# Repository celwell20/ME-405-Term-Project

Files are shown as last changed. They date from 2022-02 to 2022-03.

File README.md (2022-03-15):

# ME 405 Term Project
## Tyler McCue and Clayton Elwell Term Project

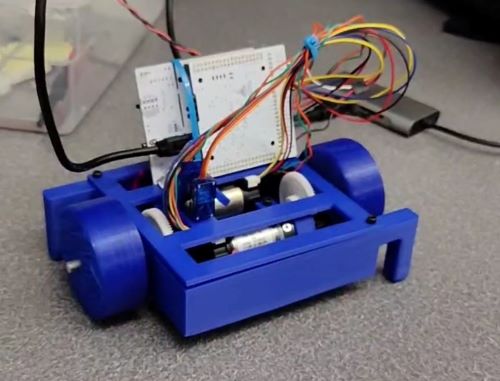
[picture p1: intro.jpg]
Intro


### Introduction
The purpose of this device is to draw a 2D image that may be determined by the user, or an appropriate
.hpgl interpreter. The device was not designed for a particular use case, rather as a novel mechatronic
system that can perform the desired task. Design constraints for this project included the project budget
and system complexity.

### Hardware
To address the small project budget, we sourced most of our hardware components from the various scrap piles
around the mechatronics lab. The large system components such as the wheel and chassis were 3D printed so that
we may iterate rapidly if need be. The only purchased components for this project are the bearings that
facilitate the wheels’ motion.

The system relies on two Pittman motors to actuate corresponding wheels that are linked via a simple gear train,
as seen in Figure 1. The wheels are 3D printed from TPU to increase friction and improve positional accuracy;
the chassis is fabricated from PLA. The two pegs on either side of the chassis help the car balance and prevent
the need for any software to balance the wheels with the motor torques (Figure 2). Two bearings facilitate each wheel’s
rotation, and the driveshafts are cut from 0.25” steel rod stock that was found in the mechatronics lab (Figure 3).

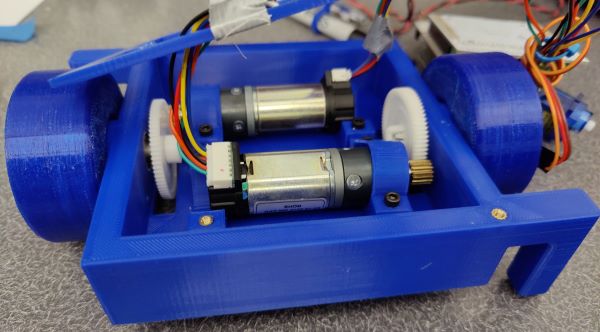
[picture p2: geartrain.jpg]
Pittman

<br>
Figure 1. Torque transmission system.

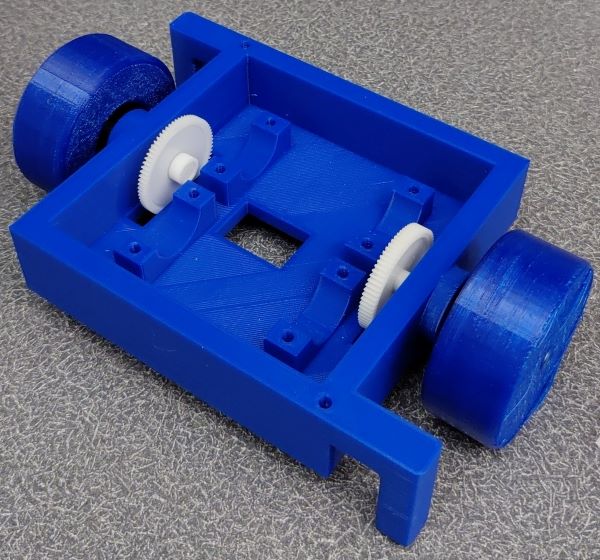
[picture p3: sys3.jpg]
Chassis

<br>
Figure 2. Chassis and wheels.

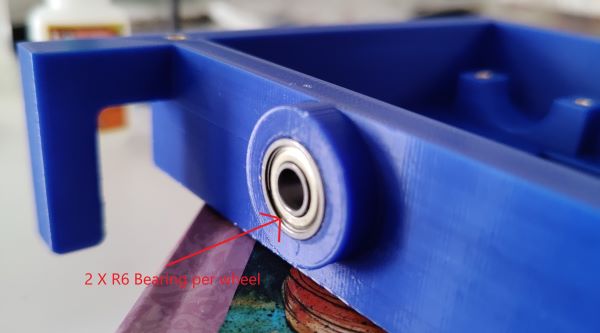
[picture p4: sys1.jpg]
Bearings

<br>
Figure 3. Press-fit bearings (with superglue).

To connect the motors to the chassis, M3 heat-set inserts and machine screws were used with PLA “straps” as
seen in Figure 1 (PLA straps) and 4 (heat-set inserts).

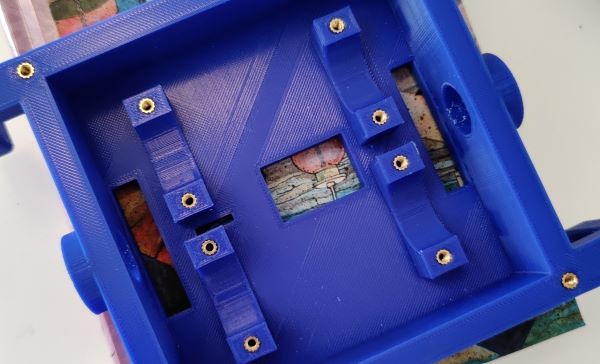
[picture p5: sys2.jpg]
Inserts

<br>
Figure 4. Chassis heat set inserts.

A Tower Pro servo motor is used control the drawing apparatus’s contact with the sketching surface; it is
press fit into a thin PLA plate that fastens to the chassis with M3 heat-set inserts and machine screws (Figure 5).

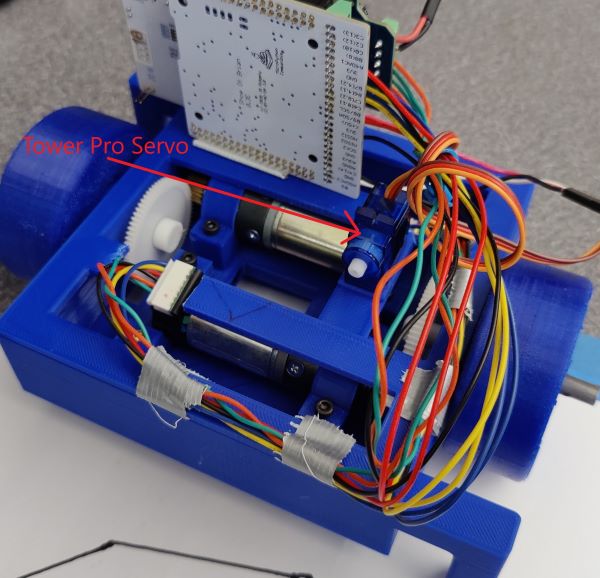
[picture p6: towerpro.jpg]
Tower

<br>
Figure 5. Drawing apparatus servo motor.

The electronic hardware for this system includes the two ME 405 Pittman BLDC motors, a Tower Pro servo motor
from any common Arduino starter kit, a Nucleo with the Shoe of Brian and motor driver/shoe, and a portable
charger (optional). The portable charger replaced our original intent of using an RC battery, because the
portable charger had a convenient 5V power output, and it was free. The harness was a rudimentary combination
of strategically placed zip ties and duct tape strips.

### Software
The software takes a series of G-code-esque commands and converts those commands to a corresponding rotation
for each wheel to rotate through. More specifically, the commands are a combination of degrees to rotate and
inches to translate, with a Boolean input to indicate whether the pen should be “up” or “down”.

Ex:
r10-d5-p0 (Moves plotter 20 degrees clockwise, and 5 inches forward with the pen up)

We utilized a closed-loop proportional controller with feedback from the Pittman motor encoders to command the
car to travel to the desired angle. A co-task program was then used to control both motors semi synchronously.
Our firmware may be referenced in the "src" directory and documentation maybe found in the following
link: https://celwell20.github.io/ME-405-Term-Project/

### Results
We tested our system by giving it various instructions to execute. First, we modeled a drawing in SOLIDWORKS to
obtain accurate rotation and translation coordinates to create our drawing instructions. It should be noted that
some sort of interpreter could be created to perform this task automatically; we decided that such a tool was
outside the scope of this project. Once we had a set of instructions, we uploaded them to the Nucleo’s flash
memory and prompted our system to execute the instructions. Figure 6 displays the desired drawing created in
SOLIDWORKS; Figure 6 displays the drawing created by our system. Figure 8 links to a video demonstration of our
plotter car.

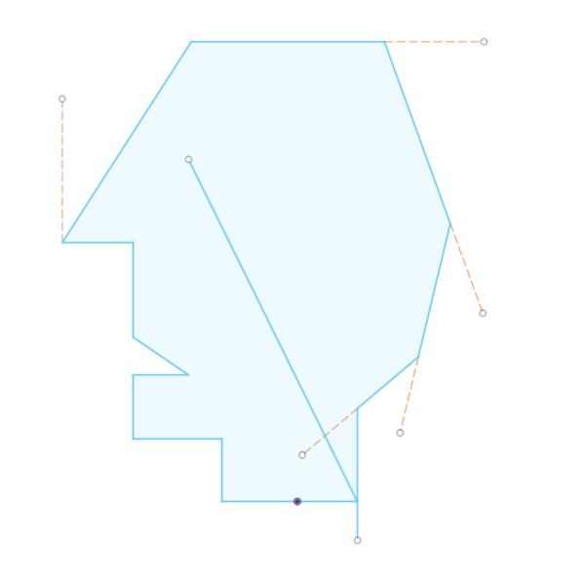
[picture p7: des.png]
des

<br>
Figure 6. Desired drawing.

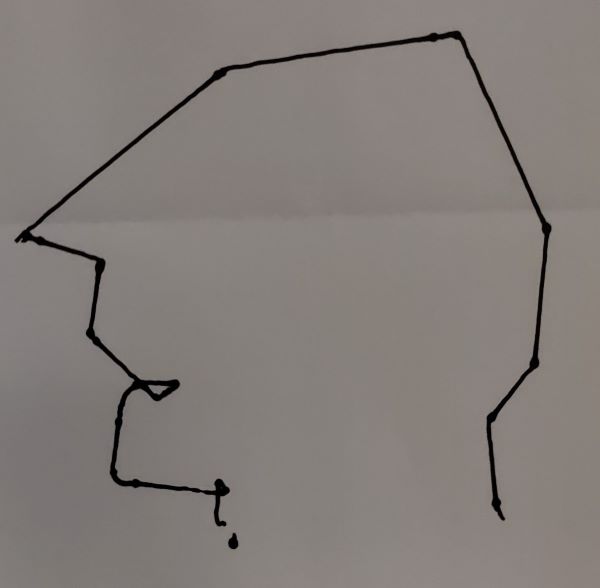
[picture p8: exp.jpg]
exp

<br>
Figure 7. Our system's drawing.

ME 4005 Term Project Demo (https://www.youtube.com/watch?v=QUkxFrMt-7k "ME 405 Term Project Demo")
<br>
Figure 8. Demonstration video link.

### Discussion
We learned that a two-wheeled car is a decent approach to creating a plotter tool. Our system’s simplicity allowed
us to dedicate equal time to the fabrication of the system and development of the controller and drawing
instruction interpreter. Our selection of simple hardware components resulted in few hardware debugging issues
and allowed us to conduct extensive testing throughout the system design process.

Areas for possible improvement include creating an interpreter than can convert a SOLIDWORKS drawing file to a
sequence of commands that our plotter car can subsequently execute. A more robust wire harness could also be
developed if this system were to be designed with commercialization in mind.

## Additional Contents and Files

### Kinematic Derivation
The following calculations derive the relationship between the angle of the motor shaft and the angle of the corresponding wheel. <br>
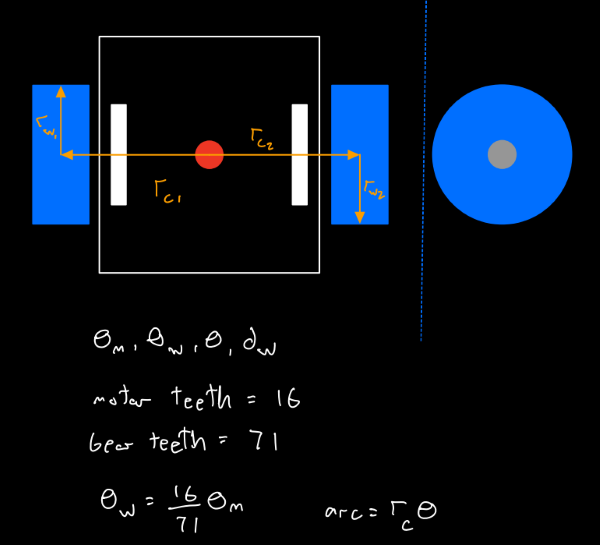
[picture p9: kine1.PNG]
kinematics1

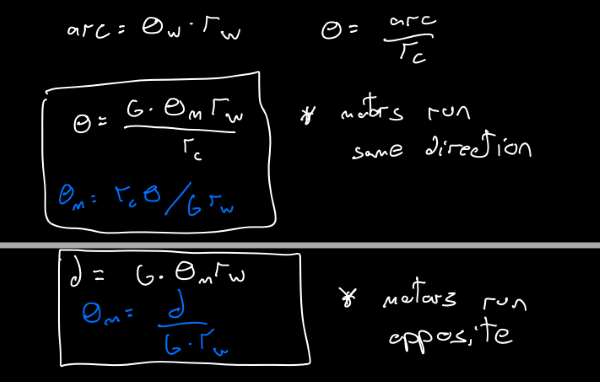
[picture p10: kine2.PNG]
kinematics2


### Bill of Materials

| Qty. | Part | Source | Est. Cost |
|:----:|:---|:---|:---:|
|  2 | Pittperson Gearmotors | ME405 Tub | - |
|  1 | Nucleo with Shoe | ME405 Tub | - |
|  1 | Purple Sharpie&trade; | Rite Aid&trade; | $3.00 |
|  2 | Motor Driver/Shield | ME405 Tub | - |
|  1 | ABS/PLA Filament Roll | Tyler's Closet | - |
|  2 | TPU Wheels | Craig K's Closet | - |
|  2 | Wheel axel | Mechatronics Lab | - |
|  2 | Gears | Mechatronics Lab | - |
|  1 | Tower Pro Servo Motor | Tyler's Closet | - |
|  1 | 5V Portable Charger | Tyler's Closet | - |
|  4 | R6 Bearings | Amazon | $8.47 |
|  10  | M3 Heat Set Inserts | Clayton's Closet | - |
|  10  | M3 10 mm SCHS | Clayton's Closet | - |

### SOLIDWORKS Models and Assemblies
CAD models may be referenced in the “SOLIDWORKS Model” directory.
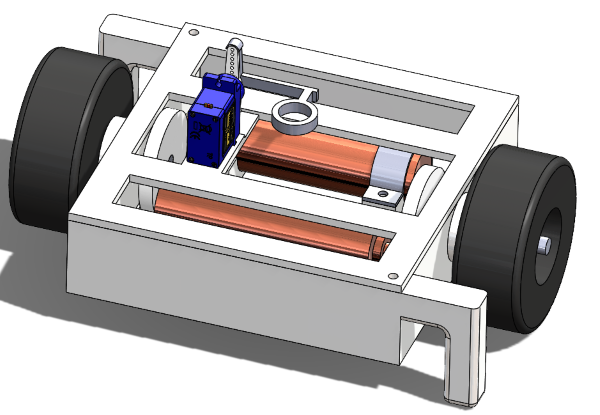
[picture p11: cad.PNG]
Isometric view of system


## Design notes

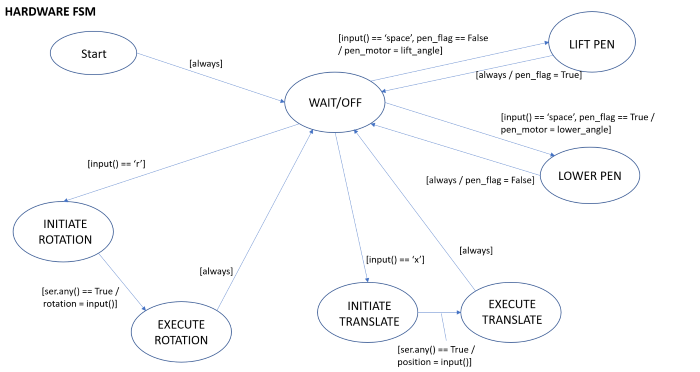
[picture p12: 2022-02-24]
Images/hardware_fsm.PNG

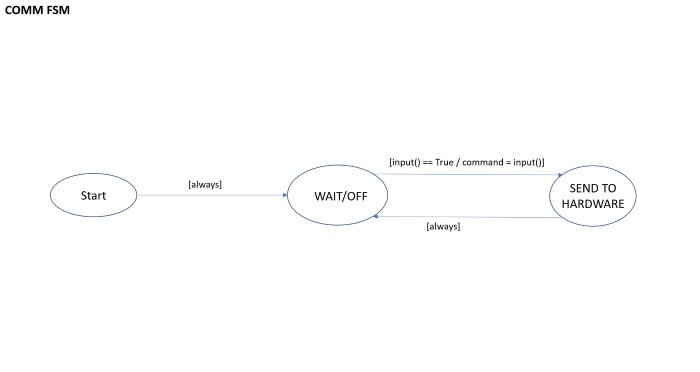
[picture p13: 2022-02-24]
Images/comm_fsm.PNG

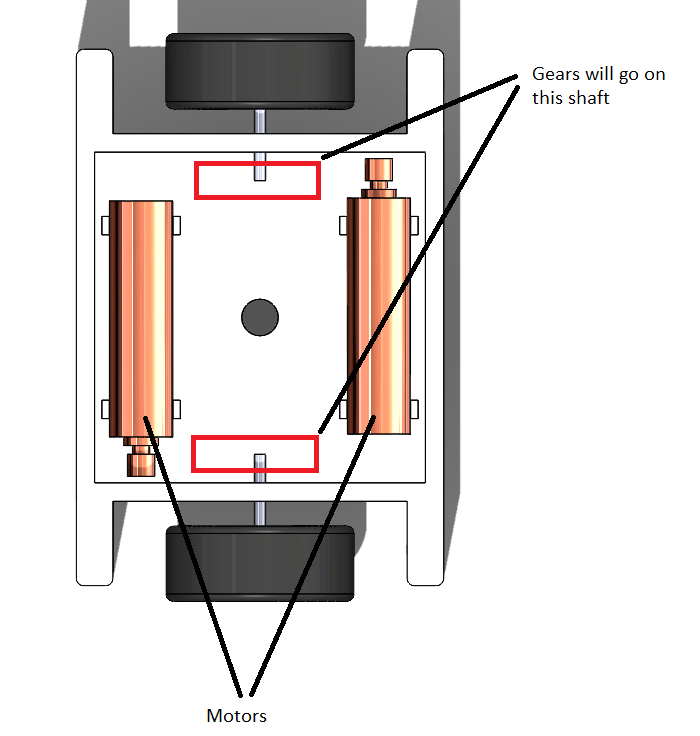
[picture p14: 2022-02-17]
motorlayout.PNG

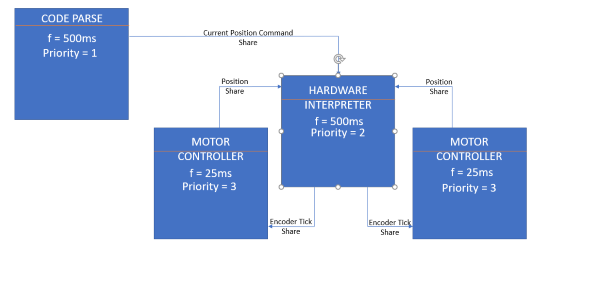
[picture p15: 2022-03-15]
Images/task_diagram.png

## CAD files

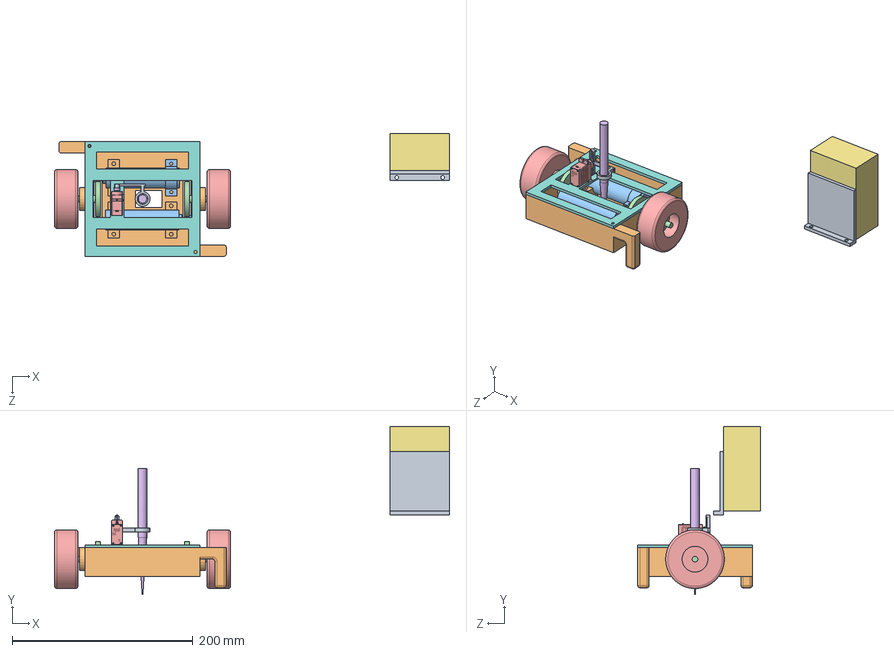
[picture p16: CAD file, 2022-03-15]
SOLIDWORKS Model/system assembly.SLDASM
437.2 x 186.5 x 135.8 mm
frame base
pittman motor x 2
wheel axel x 2
wheel x 2
nucleo_shield_shoe
Electronics housing^system assembly
nucleo adapter
60355K503_Ball Bearing x 4
94459A140_BRASS HEAT-SET INSERT FOR PLASTIC x 2
Part1^system assembly
gear1 x 2
SG90 - Micro Servo 9g - Tower Pro.1
SG90 - Micro Servo 9g - Tower Pro.3
SG90 - Micro Servo 9g - Tower Pro.5
SG90 - Micro Servo 9g - Tower Pro.6
Part2^servo_penmount

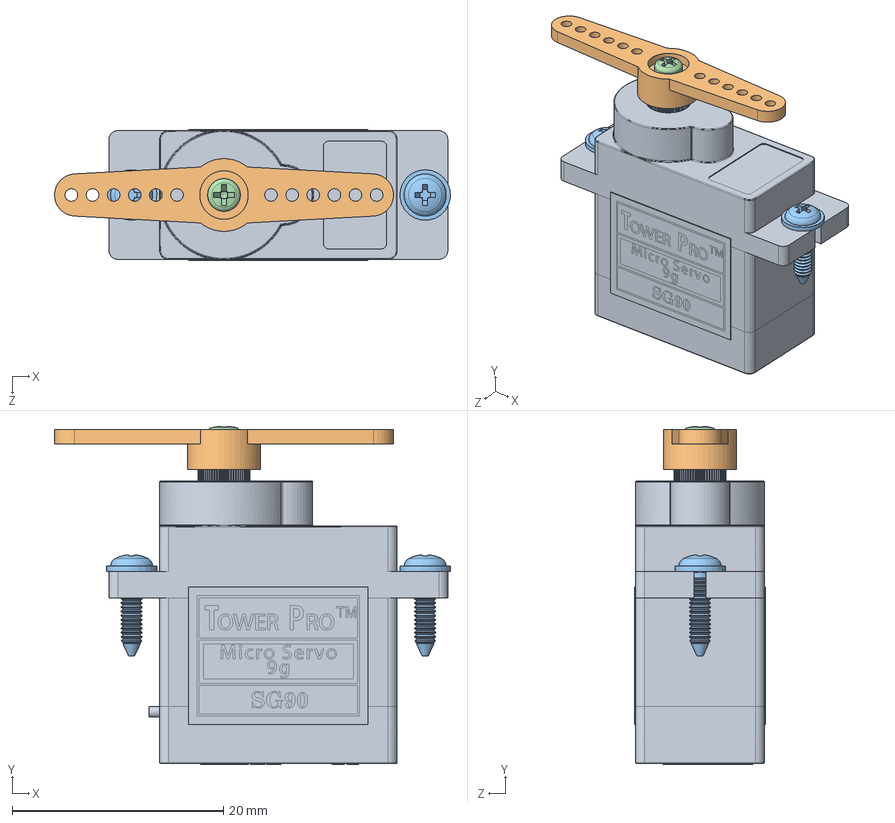
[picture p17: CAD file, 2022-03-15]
SOLIDWORKS Model/servo/microservo files/SG90 - Micro Servo 9g - Tower Pro.SLDASM
37.5 x 32.0 x 12.4 mm
SG90 - Micro Servo 9g - Tower Pro.1
SG90 - Micro Servo 9g - Tower Pro.3
SG90 - Micro Servo 9g - Tower Pro.5 x 2
SG90 - Micro Servo 9g - Tower Pro.6

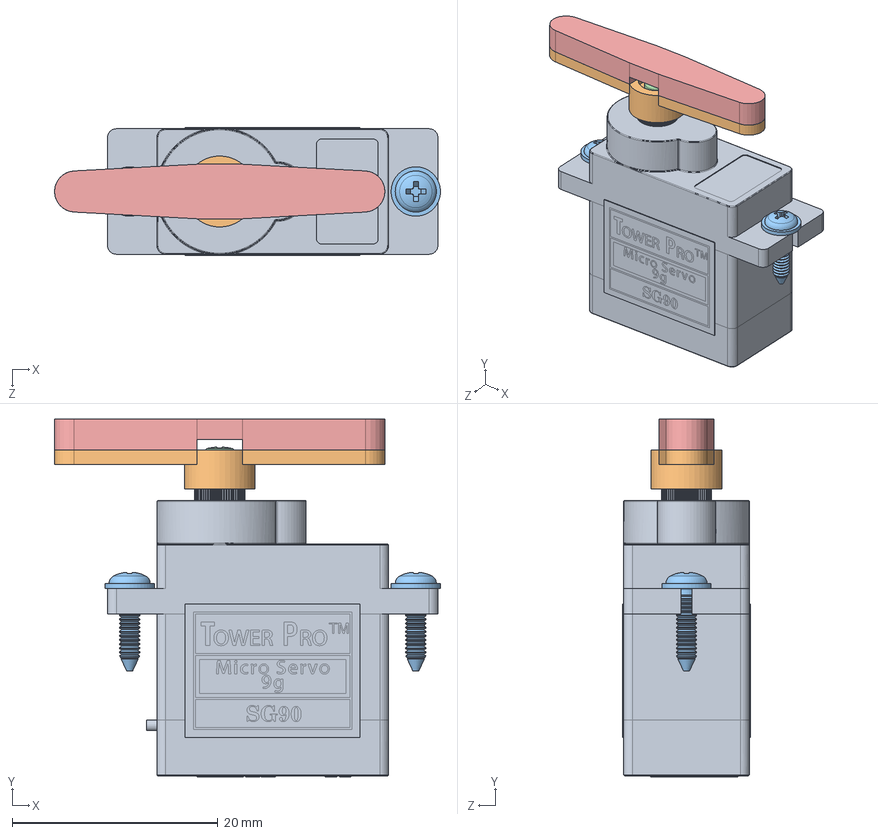
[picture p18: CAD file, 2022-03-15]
SOLIDWORKS Model/servo_penmount.SLDASM
37.5 x 34.8 x 12.4 mm
SG90 - Micro Servo 9g - Tower Pro.1
SG90 - Micro Servo 9g - Tower Pro.3
SG90 - Micro Servo 9g - Tower Pro.5 x 2
SG90 - Micro Servo 9g - Tower Pro.6
Part2^servo_penmount

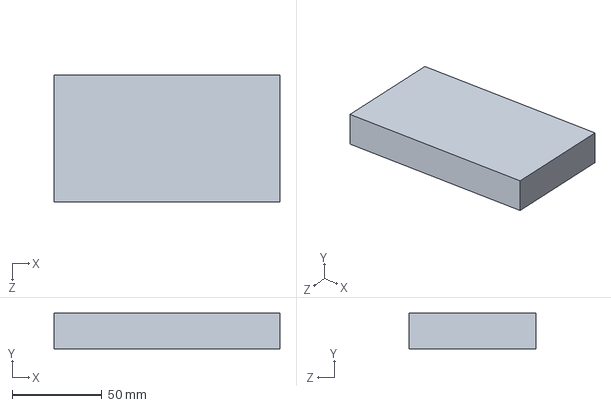
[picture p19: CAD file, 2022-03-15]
SOLIDWORKS Model/battery.SLDPRT
126.0 x 20.0 x 71.0 mm

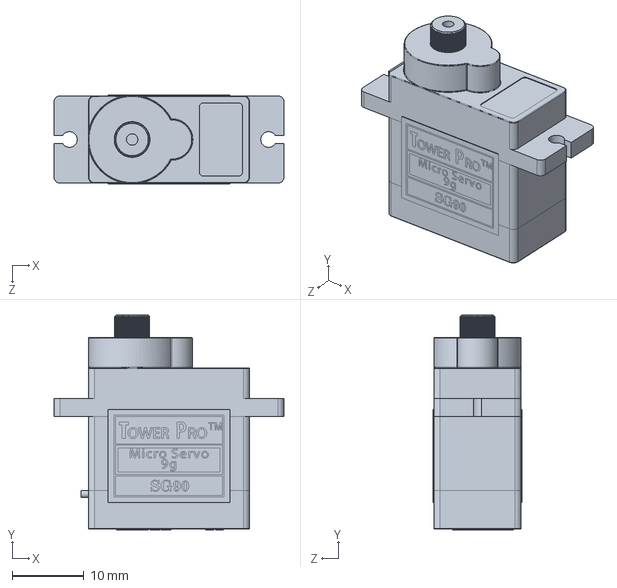
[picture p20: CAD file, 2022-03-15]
SOLIDWORKS Model/servo/microservo files/SG90 - Micro Servo 9g - Tower Pro.1.SLDPRT
32.1 x 30.0 x 12.4 mm

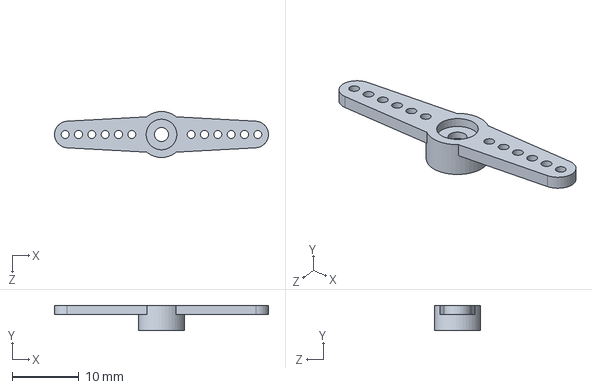
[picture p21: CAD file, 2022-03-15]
SOLIDWORKS Model/servo/microservo files/SG90 - Micro Servo 9g - Tower Pro.3.SLDPRT
32.1 x 3.80 x 6.90 mm

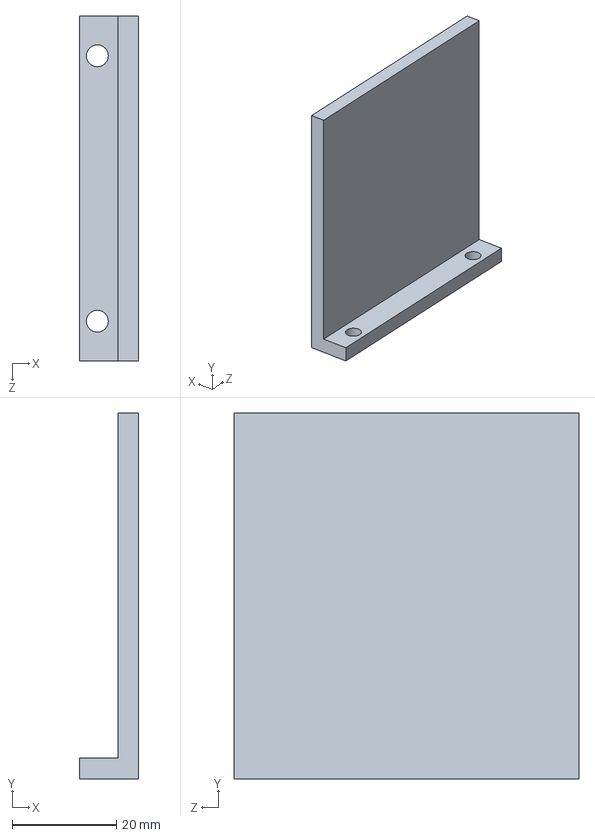
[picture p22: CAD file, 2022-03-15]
SOLIDWORKS Model/nucleo adapter.SLDPRT
11.4 x 70.0 x 66.0 mm

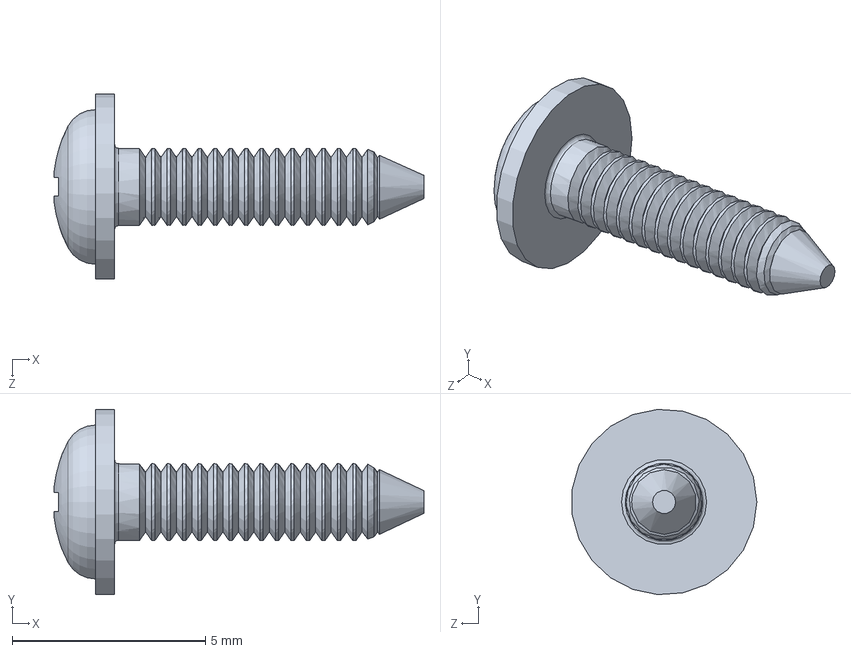
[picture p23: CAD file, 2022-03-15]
SOLIDWORKS Model/servo/microservo files/SG90 - Micro Servo 9g - Tower Pro.5.SLDPRT
9.57 x 4.79 x 4.78 mm

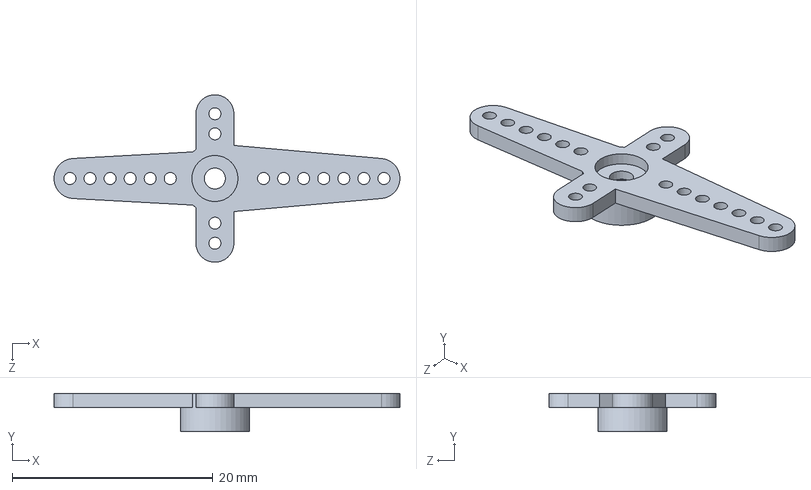
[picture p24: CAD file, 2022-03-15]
SOLIDWORKS Model/servo/microservo files/SG90 - Micro Servo 9g - Tower Pro.4.SLDPRT
34.5 x 3.80 x 16.7 mm

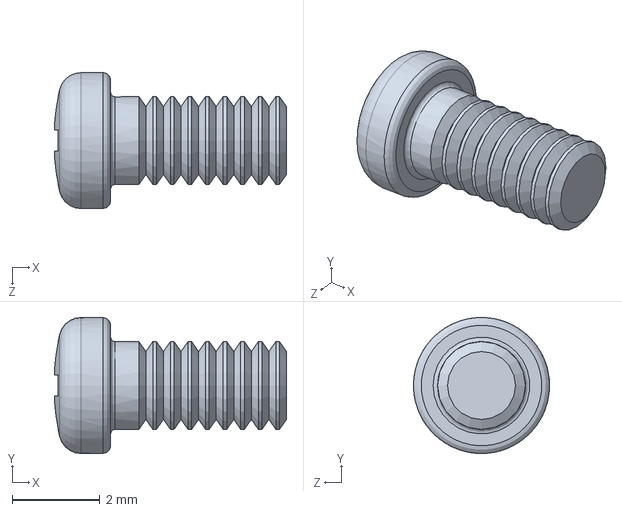
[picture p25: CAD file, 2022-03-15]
SOLIDWORKS Model/servo/microservo files/SG90 - Micro Servo 9g - Tower Pro.6.SLDPRT
5.28 x 3.10 x 3.10 mm

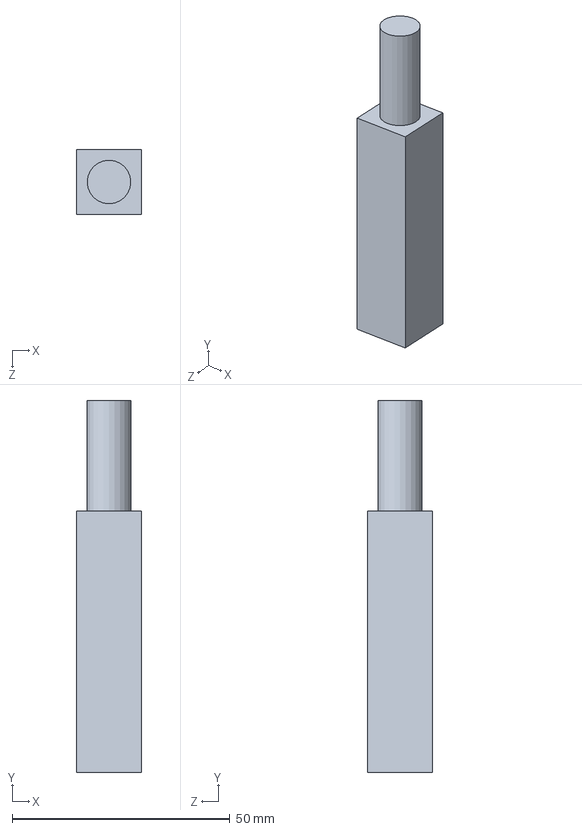
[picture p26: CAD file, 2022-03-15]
SOLIDWORKS Model/solenoid.SLDPRT
15.0 x 85.4 x 15.0 mm

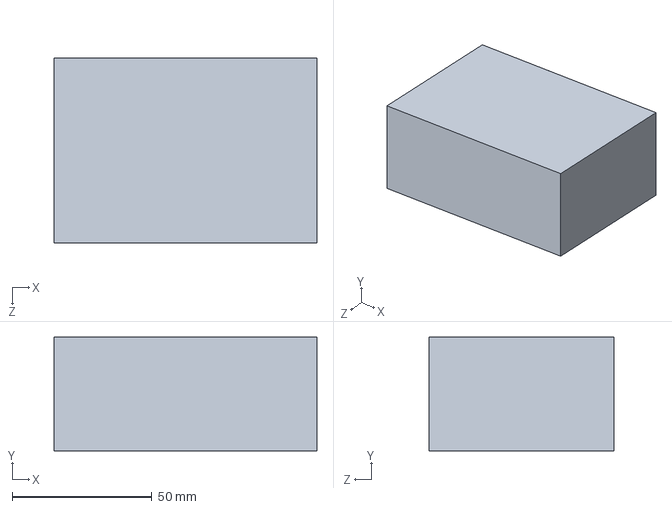
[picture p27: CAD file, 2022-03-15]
SOLIDWORKS Model/nucleo_shield_shoe.SLDPRT
94.0 x 40.6 x 66.0 mm

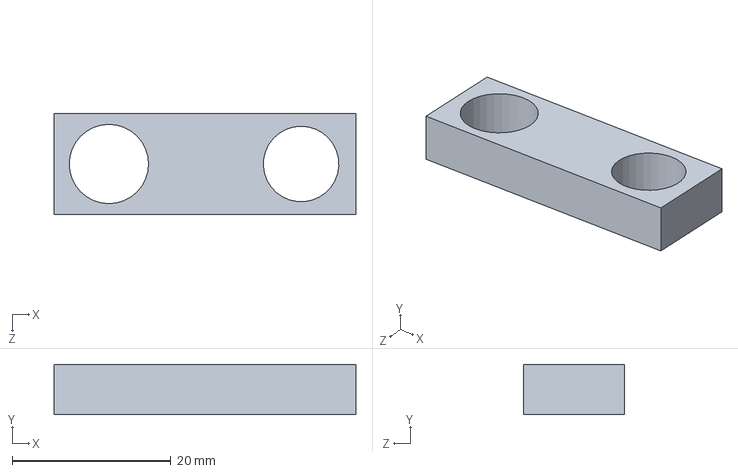
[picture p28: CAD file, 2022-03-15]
SOLIDWORKS Model/pen adapter.SLDPRT
38.1 x 6.35 x 12.7 mm

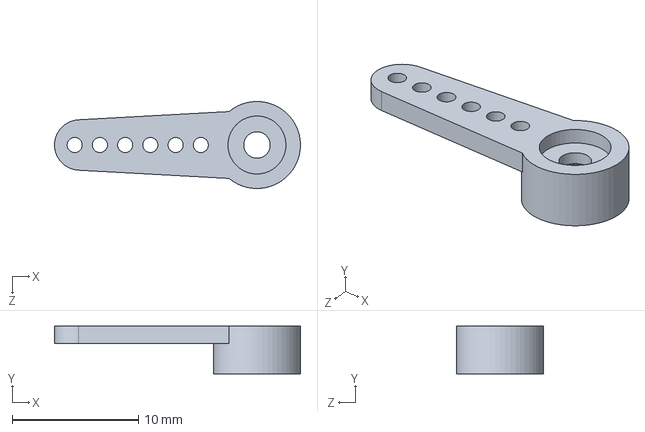
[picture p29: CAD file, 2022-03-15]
SOLIDWORKS Model/servo/microservo files/SG90 - Micro Servo 9g - Tower Pro.2.SLDPRT
19.5 x 3.80 x 6.90 mm

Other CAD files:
SOLIDWORKS Model/frame base.SLDPRT
SOLIDWORKS Model/pittman motor.SLDPRT
SOLIDWORKS Model/gear1.SLDPRT
SOLIDWORKS Model/wheel axel.SLDPRT
SOLIDWORKS Model/60355K503_Ball Bearing.SLDPRT
SOLIDWORKS Model/7804K101_Stainless Steel Ball Bearing.SLDPRT
SOLIDWORKS Model/94459A140_BRASS HEAT-SET INSERT FOR PLASTIC.SLDPRT
SOLIDWORKS Model/pen.SLDPRT
SOLIDWORKS Model/servo/microservo files/SG90 - Micro Servo 9g - Tower Pro.x_t
SOLIDWORKS Model/wheel.SLDPRT
SOLIDWORKS Model/wheel.STL

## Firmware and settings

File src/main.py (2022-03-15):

"""!
@file main.py
    This file is the main program file for the plotter car.
    File creates several tasks including motor, interpreter tasks, and
    file parsing tasks.

@author         Clayton Elwell
@author         Tyler McCue
@date           March 4, 2022
"""

import gc
import pyb
import cotask
import task_share
import Closed_Loop as control
import encoder_elwell_mccue as enc
import motor_elwell_mccue as moe
import utime
import servo_driver as ser
import chassis_driver as ch


def task_MCU1 ():
    """!
    Task controls motor 1 
    """
    while True:
        update1 = enc1.update()
        duty1 = control1.run(update1)
        motor1.set_duty_cycle(duty1)
        if abs(duty1) <= 20 and enc1.get_delta() < 5:
            share_ready1.put(1)
        if share_ready1.get() == 1 and share_ready2.get() == 1:
            share_bothR.put(1)
        yield (0)


def task_MCU2 ():
    """!
    Task controls motor 2.
    """
    while True:
        update2 = enc2.update()
        duty2 = control2.run(update2)
        motor2.set_duty_cycle(duty2)
        if abs(duty2) <= 20 and enc2.get_delta() < 5:
            share_ready2.put(1)
        if share_ready1.get() == 1 and share_ready2.get() == 1:
            share_bothR.put(1)
        yield (0)
        
def task_interpret ():
    """!
    Task interprets commands from file to control certain motors
    """
    while True:
        if share_bothR.get() == 1:
            if share_comm.get() == 0:
                (ref1, ref2) = chass.find_motor_dists(True, share_theta.get())
                control1.setReference(ref1)
                control2.setReference(ref2)
                enc1.set_position(0)
                enc2.set_position(0)
                share_bothR.put(0)
                share_ready2.put(0)
                share_ready1.put(0)
            if share_comm.get() == 1:
                servo.change_pen(share_pen.get())
                (ref1, ref2) = chass.find_motor_dists(False, share_dist.get())
                control1.setReference(ref1)
                control2.setReference(ref2)
                enc1.set_position(0)
                enc2.set_position(0)
                share_bothR.put(0)
                share_ready2.put(0)
                share_ready1.put(0)
            if share_comm.get() == 2:
                share_nextI.put(1)
            share_comm.put(share_comm.get() + 1)
            if share_comm.get() > 2:
                share_comm.put(0)
        yield(0)
            

def task_parse ():
    """!
    Task parses file for commands
    """
    with open(r"code.txt", "r") as c:
        while True:
            if share_nextI.get() == 1:
                commands = c.readline()
                if "st" in commands:
                    share_stop.put(1)
                else:    
                    if len(commands) > 0:
                         commands = commands.split("_")
                         share_theta.put(float(commands[0][1:]))
                         share_dist.put(float(commands[1][1:]))
                         share_pen.put(float(commands[2][1:]))
            share_nextI.put(0)
            yield(0)
                
        
# This code creates all motor, encoder, control, servo, and chassis objects and instantiates 4 tasks to control the robot
#

if __name__ == "__main__":
    ## Right wheel tuning parameter
    right = 1.01
    ## Left wheel tuning parameter
    left = 1.01
    ## Chassis tuning parameter
    tune = 1.02
    ## Pen POC to wheel distance
    center = 3.03
    ## Wheel radius
    wheel = 2.53/2
    ## Gear ratio
    gear = 16/71
    ## Encoder conversion factor
    encoder = (256*16*4/360)

    ##Driver for chassis
    chass = ch.chassis(center, wheel, gear, encoder, tune, right, left)
    
    ##Driver for servo object
    servo = ser.Servo(2, pyb.Pin(pyb.Pin.cpu.B3, pyb.Pin.OUT_PP))
    
    ## Driver object for first motor
    motor1 = moe.MotorDriver(pyb.Pin.cpu.A10, pyb.Pin.cpu.B4, pyb.Pin.cpu.B5, 3)
    
    ## Driver object for second motor
    motor2 = moe.MotorDriver(pyb.Pin.cpu.C1, pyb.Pin.cpu.A0, pyb.Pin.cpu.A1, 5)
    
    ## Driver object for first encoder
    enc1 = enc.EncoderDriver(pyb.Pin.cpu.B6, pyb.Pin.cpu.B7, 4)
    ## Driver object for second encoder
    enc2 = enc.EncoderDriver(pyb.Pin.cpu.C6, pyb.Pin.cpu.C7, 8)
    
    motor1.enable()
    motor2.enable()
    
    enc1.set_position(0)
    enc2.set_position(0)
    
    ## Controller object for first motor
    control1 = control.ClosedLoop(-100, 100, .009, 0, 0)
    ## Controller object for second motor
    control2 = control.ClosedLoop(-100, 100, .009, 0, 0)
    
    

    # Create a shares for tasks
    ## Share to ensure motor 1 is at the correct position
    share_ready1 = task_share.Share ('f', thread_protect = False, name = "Ready1")
    ## Share to ensure motor 2 is at the correct position
    share_ready2 = task_share.Share ('f', thread_protect = False, name = "Ready2")
    ## Share to ensure both motors are at the correct position
    share_bothR = task_share.Share ('f', thread_protect = False, name = "Ready2")
    ## Share storing commands between PC and Nucleo
    share_comm = task_share.Share ('f', thread_protect = False, name = "Command")
    ## Share storing next instruction for plotter tool to execute
    share_nextI = task_share.Share ('f', thread_protect = False, name = "Stop")
    
    #share_c1val = task_share.Share ('f', thread_protect = False, name = "Val1")
    
    #share_c2val = task_share.Share ('f', thread_protect = False, name = "Val2")
    ## Current controller gain value
    share_currC = task_share.Share ('f', thread_protect = False, name = "CurrentCommand")
    ## Rotational distance for motors to travel
    share_theta = task_share.Share ('f', thread_protect = False, name = "ThetaVal")
    ## Wheel radius shared value
    share_dist = task_share.Share ('f', thread_protect = False, name = "RadiusVal")
    ## Boolean indicating whether pen should be up or down
    share_pen = task_share.Share ('f', thread_protect = False, name = "PenVal")
    ## Stores value that stops the plotter device
    share_stop = task_share.Share ('f', thread_protect = False, name = "Stop")
    
    
    share_ready1.put(0)
    share_ready2.put(0)
    share_currC.put(0)
    share_stop.put(0)
    share_nextI.put(1)
    share_comm.put(0)
    share_bothR.put(1)
    

    # Create the tasks. If trace is enabled for any task, memory will be
    # allocated for state transition tracing, and the application will run out
    # of memory after a while and quit. Therefore, use tracing only for 
    # debugging and set trace to False when it's not needed
    ## Motor 1 Task
    task1 = cotask.Task (task_MCU1, name = 'Task_Motor_1', priority = 3, 
                         period = 25, profile = True, trace = False)
    ## Motor 2 Task
    task2 = cotask.Task (task_MCU2, name = 'Task_Motor_2', priority = 3, 
                         period = 25, profile = True, trace = False)
    ## Interpreter Task
    task3 = cotask.Task (task_interpret, name = 'Task_Interpreter', priority = 2, 
                         period = 500, profile = True, trace = False)
    ## Parser Task
    task4 = cotask.Task (task_parse, name = 'Task_Parser', priority = 1, 
                         period = 500, profile = True, trace = False)
    
    cotask.task_list.append (task1)
    cotask.task_list.append (task2)
    cotask.task_list.append (task3)
    cotask.task_list.append (task4)

    # Run the memory garbage collector to ensure memory is as defragmented as
    # possible before the real-time scheduler is started
    gc.collect ()
    
    while share_stop.get() == 0:
        cotask.task_list.pri_sched()
        
    motor1.set_duty_cycle(0)
    motor2.set_duty_cycle(0)
    motor1.disable()
    motor2.disable()

    
            
        

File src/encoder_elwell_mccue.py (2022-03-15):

"""@file           encoder_elwell_mccue.py
   @brief          A driver for reading from the Quadrature Encoders
   @details        The functions of this driver allow one to "get", "set", and "find" the encoder delta.
   
                   The driver creates a 16-bit timer, whose channels correlate ticks to encoder rotation. The driver also
                   has a method that is used to return encoder position and velocity to the encoder task.
   @author         Clayton Elwell
   @author         Tyler McCue
   @date           January 27, 2022
"""
import pyb

class EncoderDriver:
    '''@brief       Interface with quadrature encoder
       @details     Contains the basic functionality of an encoder that will be sent to the encoder task upon user request.
    '''

    
    def __init__(self, pin1, pin2, timerID):
        
        '''@brief       Constructs an encoder object and assigns the correct pins and timer.
           @details     Creates a 16-bit timer whose number is defined in the encoder task. The timer channels and pins are defined 
                        in the encoder task.
           @param       pin1    Pin to be used with the encoder channel 1
           @param       pin2    Pin to be used with the encoder channel 2
           @param       timerID  Timer channel to be used with the previously assigned pins.
        '''
        ## Total rotational position of the encoder, measured in ticks.
        self.position = 0
        ## Encoder position correlated to the update prior to the most recent update.
        self.position1 = 0
        ## Encoder position correlated to the most recent update
        self.position2 = 0
        ## Difference (in ticks) between the most recent encoder update and the update prior to the most recent update.
        self.delta = 0
        
        ##  Timer for CH1 and CH2 pins
        self.timX = pyb.Timer(timerID, prescaler = 0, period = 65535)
        ## Assigning the pin1 parameter to the STM32L476RG channel 1
        self.timX.channel(1, pyb.Timer.ENC_AB, pin=pin1)
        ## Assigning the pin2 parameter to the STM32L476RG channel 2
        self.timX.channel(2, pyb.Timer.ENC_AB, pin=pin2)
        
    def update(self):
        '''@brief       Updates encoder position and delta. Also sets the encoder position and returns the current encoder position.
           @return      True rotational position of the encoder.       
        '''
        self.position1 = self.position2
        self.position2 = self.timX.counter()
        self.delta = self.get_delta()
        
        if(self.delta < -32768):
            self.position += (self.delta + 65536)
        elif(self.delta > 32768):
            self.position += (self.delta - 65536)
        else: 
            self.position += self.delta
        return self.position        

    def get_position(self):
        '''@brief      Returns encoder position.
           @return     The position of the encoder shaft.
        '''
        
        return self.position

    def set_position(self, pos):
        '''@brief       Set the encoder position to the value of parameter "pos".
            
           @param pos   The new position of the encoder shaft.
        '''
        self.position = pos
        self.delta = 0
        self.timX.counter(0)
        self.position1 = 0
        self.position2 = 0
        
        
    
    def get_delta(self):
        '''@brief      Returns the difference (in ticks) between the two most recent encoder updates.
           
           @return     The change in position of the encoder shaft between
                       the two most recent updates.
        '''
        return((self.position2 - self.position1))

# if __name__ == '__main__':
#     
#     enc1 = EncoderDriver(pyb.Pin.cpu.B6, pyb.Pin.cpu.B7, 4)
#     
#     enc2 = EncoderDriver(pyb.Pin.cpu.C6, pyb.Pin.cpu.C7, 8)
#     
#     
#     while True:
#         try:
#             print('{:}, {:}'.format(enc1.update(), enc2.update()))
#             
#         except KeyboardInterrupt:
#             break

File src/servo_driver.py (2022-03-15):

"""@file           servo_driver.py
   @brief          A driver for servo motor
   @details        The driver creates a servo object and changes the arm position from two predetermined values
   @author         Clayton Elwell
   @author         Tyler McCue
   @date           March 4, 2022
"""

import pyb

class Servo:
    '''@brief       Interface with servo motor
       @details     Contains basic functionality to move servo motor from level to raised
    '''
    
    def __init__(self, timer, pin):
        '''
        @brief          Constructor for servo motor
        @param timer    Timer object used by servo for PWM
        @param pin      Pin object that carries the command to the servo
        '''
        ### Timer number for servo motor PWM
        self.timer = timer
        ### Input pin for servo PWM
        self.pin = pin
        ## Timer object for servo
        self.tim = pyb.Timer(self.timer, freq=50) # create a timer object using timer 4

        #pinB3 = pyb.Pin(pyb.Pin.cpu.B3, pyb.Pin.OUT_PP)
        ## Timer channel for servo PWM
        self.ch2 = self.tim.channel(2, pyb.Timer.PWM, pin=pin)


    def change_pen(self, value):
        '''@brief       Changes servo motor level based on given value, 1 levels motor and rest raises motor  
        '''
        if value == 1:
            self.ch2.pulse_width_percent(8) #Level
        else:
            self.ch2.pulse_width_percent(7)

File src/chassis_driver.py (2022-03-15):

"""@file           chassis_driver.py
   @brief          A driver for converting distance and angle values for two wheeled device
   @details        The functions of this driver determine encoder values for two wheeled objects.
                   The driver uses measurements to calculate the kinematics of the vehicle.
   @author         Clayton Elwell
   @author         Tyler McCue
   @date           March 4, 2022
"""

class chassis:
    '''@brief       Interface with chassis system
       @details     Contains basic kinematics for two wheeled device
    '''
    
    def __init__(self, Rc, Rw,  GearinR, encoderR, overalltune, r, l):
        '''
        @brief              Constructor for chassis
        @param Rc           Radius of chassis to wheels
        @param Rw           Radius of wheels
        @param GearinR      Gear ratio of device
        @param encoderR     Encoder ratio of encoder to one revolution
        @param overalltune  Tuning value for slippage
        @param r            Right wheel tuning parameter
        @param l            Left wheel tuning paramter
        '''
        ## Distance from the pen POC to the center of the wheel face
        self.R_Center = Rc
        ## Wheel radius
        self.R_Wheel = Rw
        ## Gear ratio
        self.Gear_Ratio = GearinR
        ## Encoder conversion factor
        self.Encoder_Ratio = encoderR
        ## Parameter to manually tune the magnitude of rotation or translation
        self.tune_t = overalltune
        ## Manual tuning parameter for left wheel
        self.left = l
        ## Manual tuning parameter for right wheel
        self.right = r
        
    def find_motor_dists(self, rotation, value):
        '''@brief       Calculates encoder value for each wheel based on command
           @return      Tuple containing encoder value for each wheel.
           @param rotation Rotational distance for wheel to travel
           @param value    Translational distance for wheel to travel
        '''
        if rotation:
            theta_m = self.tune_t*self.Encoder_Ratio*(self.R_Center*value)/(self.Gear_Ratio*self.R_Wheel)
            return (self.right*theta_m, self.left*theta_m)
        else:
            theta_m = self.Encoder_Ratio*(180*value)/(self.Gear_Ratio*self.R_Wheel*3.1415926)
            return (theta_m, -theta_m)
